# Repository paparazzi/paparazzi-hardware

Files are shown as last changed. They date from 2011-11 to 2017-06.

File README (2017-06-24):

#
#   $Id: README 6372 2010-11-07 00:50:29Z esden $
#   Copyright (C) 2004 Pascal Brisset, Antoine Drouin
#
# This file is part of paparazzi.
#
# paparazzi is free software; you can redistribute it and/or modify
# it under the terms of the GNU General Public License as published by
# the Free Software Foundation; either version 2, or (at your option)
# any later version.
#
# paparazzi is distributed in the hope that it will be useful,
# but WITHOUT ANY WARRANTY; without even the implied warranty of
# MERCHANTABILITY or FITNESS FOR A PARTICULAR PURPOSE.  See the
# GNU General Public License for more details.
#
# You should have received a copy of the GNU General Public License
# along with paparazzi; see the file COPYING.  If not, write to
# the Free Software Foundation, 59 Temple Place - Suite 330,
# Boston, MA 02111-1307, USA.  
# 

License:
--------
All PCB CAD files are released under GNU General Public License version 2 or
newer if not stated otherwise.

Older revisions:
----------------
This is a cleaned up repository that does not contain all the history of the
files. For older revisions please check the SVN repository on Savannah:
http://svn.savannah.nongnu.org/viewvc/paparazzi-hardware/trunk/?root=paparazzi

Techno:
-------
PCBs are 4 layers boards.
  They can be ordered from companies like eurocircuits (www.eurocircuits.com).
  I solder the components with a fine temperatue controlled iron. The IMU board 
  contains BGA gyros which will require some sort hot hot air method.

Tools:
  This files are produced using Eagle (www.cadsoft.de) version 4.11 for Linux.
  gerbmerge (http://claymore.engineer.gvsu.edu/~steriana/Python/gerbmerge/) is a
  free gerber panelisation tool. gerbv (http://gerbv.sourceforge.net) is a free
  gerber viewer. eagle3d ( http://www.matwei.de/doku.php?id=en:eagle3d:eagle3d )
  is a tool that allows generation of povray views of the boards.

Outputs:
  We use the eagle batch CAM processor to generate various outputs.
  type "make gerber" to generate gerber.
  type "make printable" to generate postscript and pdf. 
  they will be put in a printable subdirectory in each subdirectory. 

Directory content:
------------------
panel: 
  Contains configuration files used in conjunction with gerbmerge to produce a pannel
  to be sent to the PCB manufacturer (eurocircuits). A panel is a big PCB containing several smaller PCB.
  It allows you to choose which boards you want for your particular system.

controller: 
  This are the paparazzi controller boards.

sensors:

tools:

lib: 
  contains eagle library parts for components not found in the standard eagle library.

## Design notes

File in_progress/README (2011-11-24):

 This directory contains in progress project an some finished development board I made to test different parts

adxrs300_breakout.sch : breakout board for adxrs300 gyro evaluation
AMI_601.sch : breakout board for AMI601 magnetometer
current_probe.sch : some current sensor I don't remember about
ir_single_long.sch
ir_single_slim.sch
lipo_connector.sch
olimex_add_on.sch
pth_supply.sch
pth_supply_servos_molex.sch
pth_supply_servos.sch
test_2620.sch
test_filter.sch
test_usb_hub.sch
tiny4l_18_1_99.sch
vor_add_on.sch
xbee.sch

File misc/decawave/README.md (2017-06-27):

Decawave Modules
================

Boards:
------

 - MiniTag: A minimal weight arduino + decawave

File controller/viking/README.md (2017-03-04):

# Viking Motorsports Engine Control Unit

The latest version is `ECU v1.0` which corresponds to `v_0.2` board files.  More info can be found in https://wiki.paparazziuav.org/wiki/VMS_ECU

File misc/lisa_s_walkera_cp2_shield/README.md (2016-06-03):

This is a prototype. Current status:

* Only connectors are used, the rest is cut off.
* No decent GND connection.
* Polarity of tail rotor is reversed, need to exchange wires in the molex-connector.

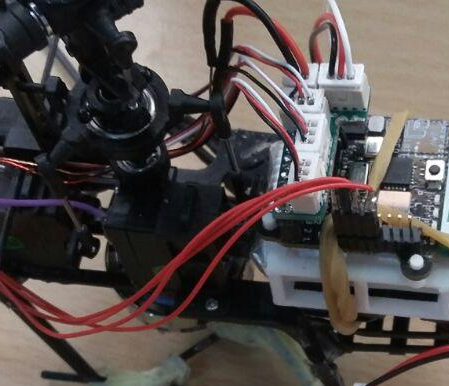
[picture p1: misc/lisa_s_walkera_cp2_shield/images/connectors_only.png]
Connectors only


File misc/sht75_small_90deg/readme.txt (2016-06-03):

Adapter board for the Sensirion SHT75 digital humidity and temperature
sensor, 90 degrees through-hole version.

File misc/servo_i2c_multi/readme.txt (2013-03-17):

This board combines a MS5611 pressure sensor, a multi-I2C connector, a 3.3V to 5V I2C level shifter and a JR servo connector.

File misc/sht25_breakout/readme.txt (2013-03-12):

Adapter board for the Sensirion SHT21/25 digital humidity and temperature
sensor.

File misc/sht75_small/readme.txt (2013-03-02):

Adapter board for the Sensirion SHT75 digital humidity and temperature
sensor.

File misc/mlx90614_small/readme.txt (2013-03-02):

Sensor board for Melexis MLX90614 infrared thermometer.

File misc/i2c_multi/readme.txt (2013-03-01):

This board is designed to connect multiple I2C sensors to one autopilot.
It was mainly used in meteorological applications.

R1 and R2 are optional and should not be populated if the autopilot is
already equipped with pull-up resistors (as in Tiny/TWOG/Lisa/...).

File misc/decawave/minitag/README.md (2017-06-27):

DM1000 + Arduino Mini Pro 3.3V/8MHz
===================================

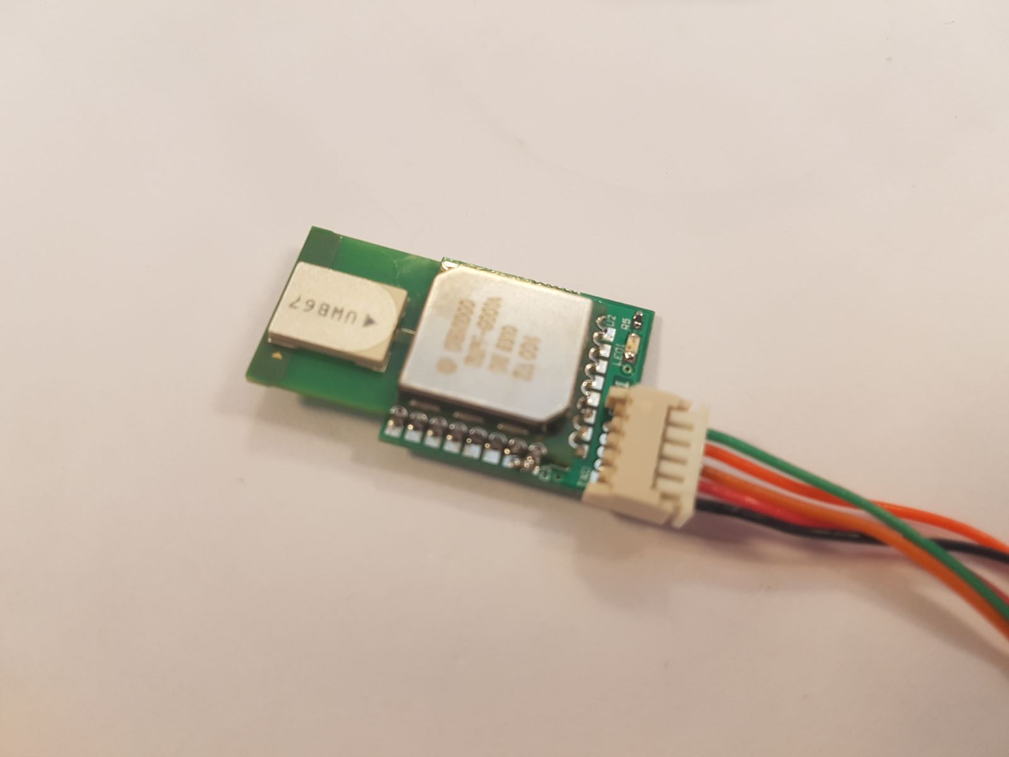
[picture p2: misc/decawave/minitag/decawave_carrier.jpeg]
Decawave Arduino


Discription:
-----------

 - Arduino Mini Pro 3.3V
 - flash elf file (bootloader+fuses) via ISP
 - afterwards the board can be programmed via arduino via serial
 - See schematics for Arduino pin numbers
 - See gerber for production

Licence:
--------

 - Hardware is released under **CC-BY-SA**

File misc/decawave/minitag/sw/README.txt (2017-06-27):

DECAWAVE ARDUINO
----------------

Arduino PRO Mini 328P 8MHz

---------

IRQ = 2

RST = 9

CS = 10
MOSI = 11
MISO = 12
SCK = 13

LED = 14 (A0)

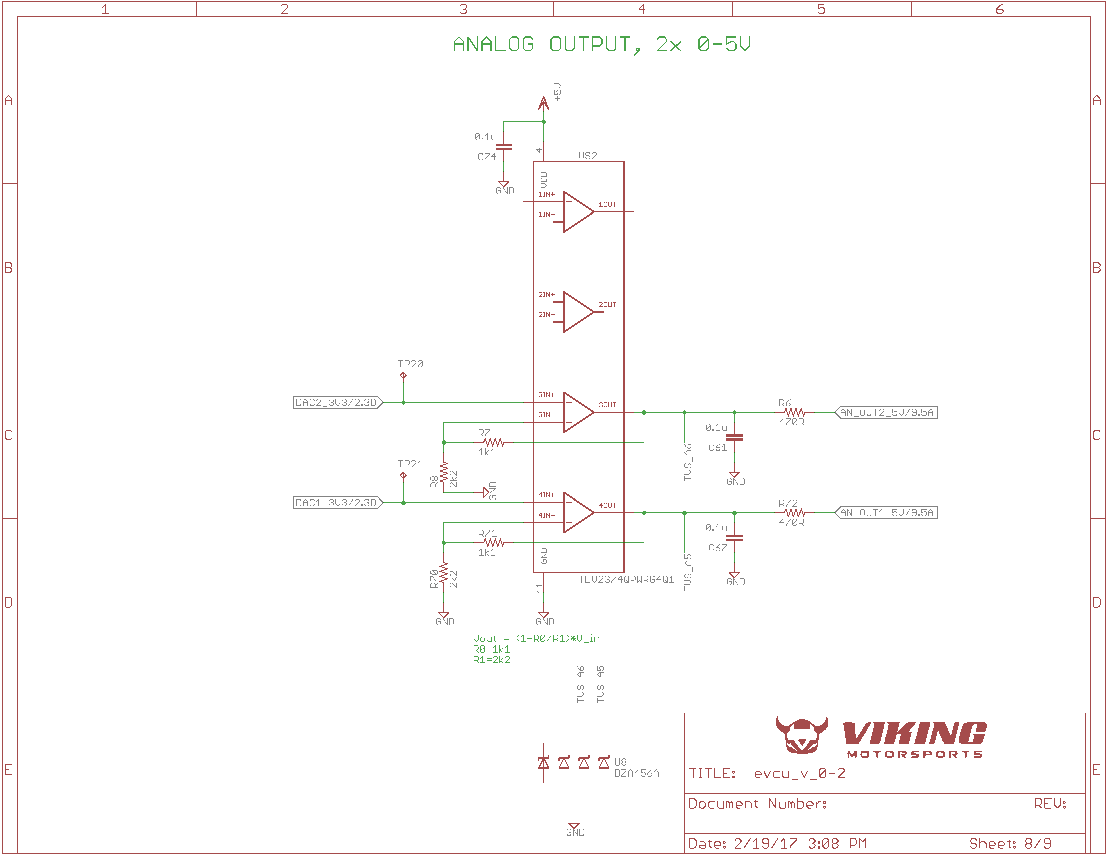
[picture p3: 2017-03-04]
controller/viking/Schematics/ecu_schematics_8.png

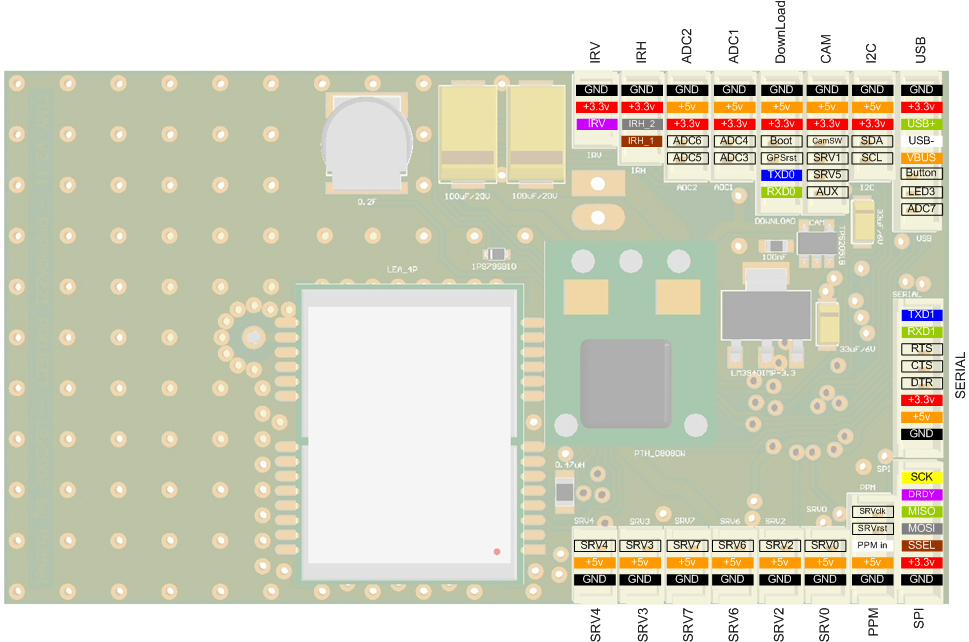
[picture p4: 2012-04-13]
controller/tiny/v2.11/Assembly/Tiny_v2-11_pinout.png

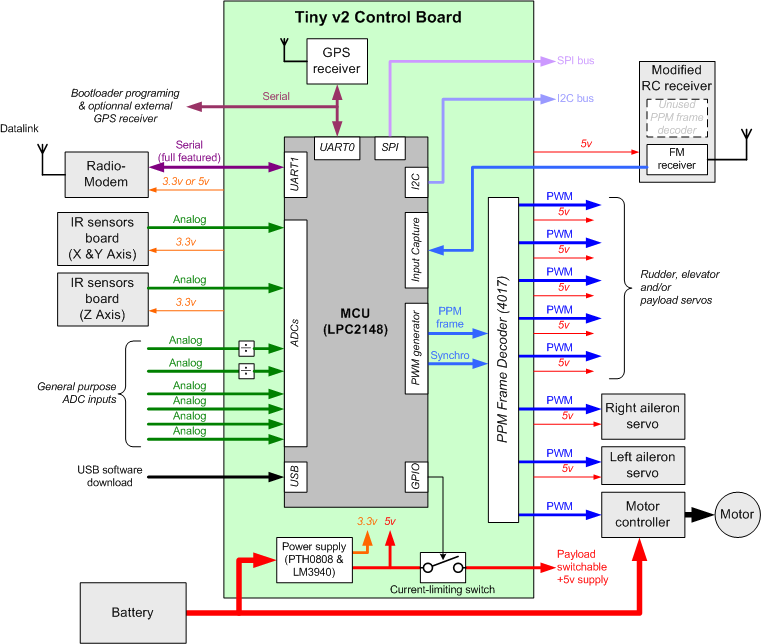
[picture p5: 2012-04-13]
controller/tiny/v2.11/Tiny_v2_11_Architecture.png

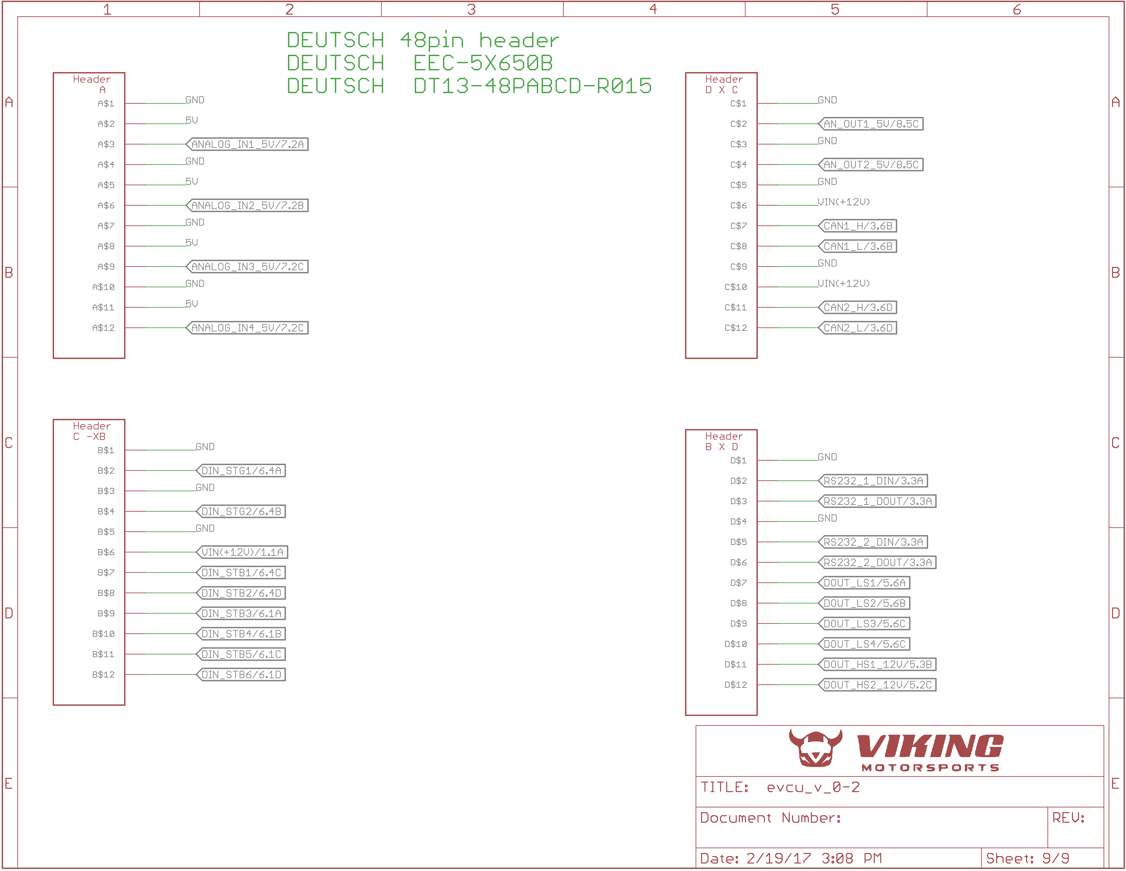
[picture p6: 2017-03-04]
controller/viking/Schematics/ecu_pinout.png

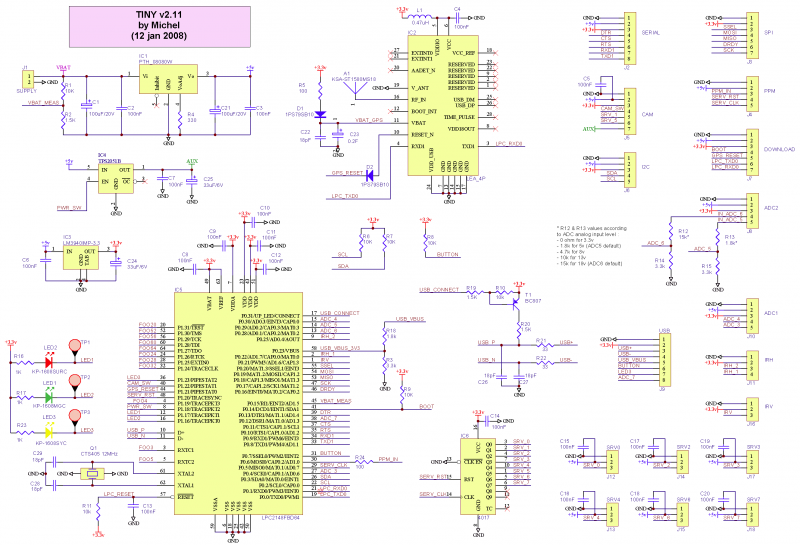
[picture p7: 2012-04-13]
controller/tiny/v2.11/Tiny_v2-11_Schematic.png

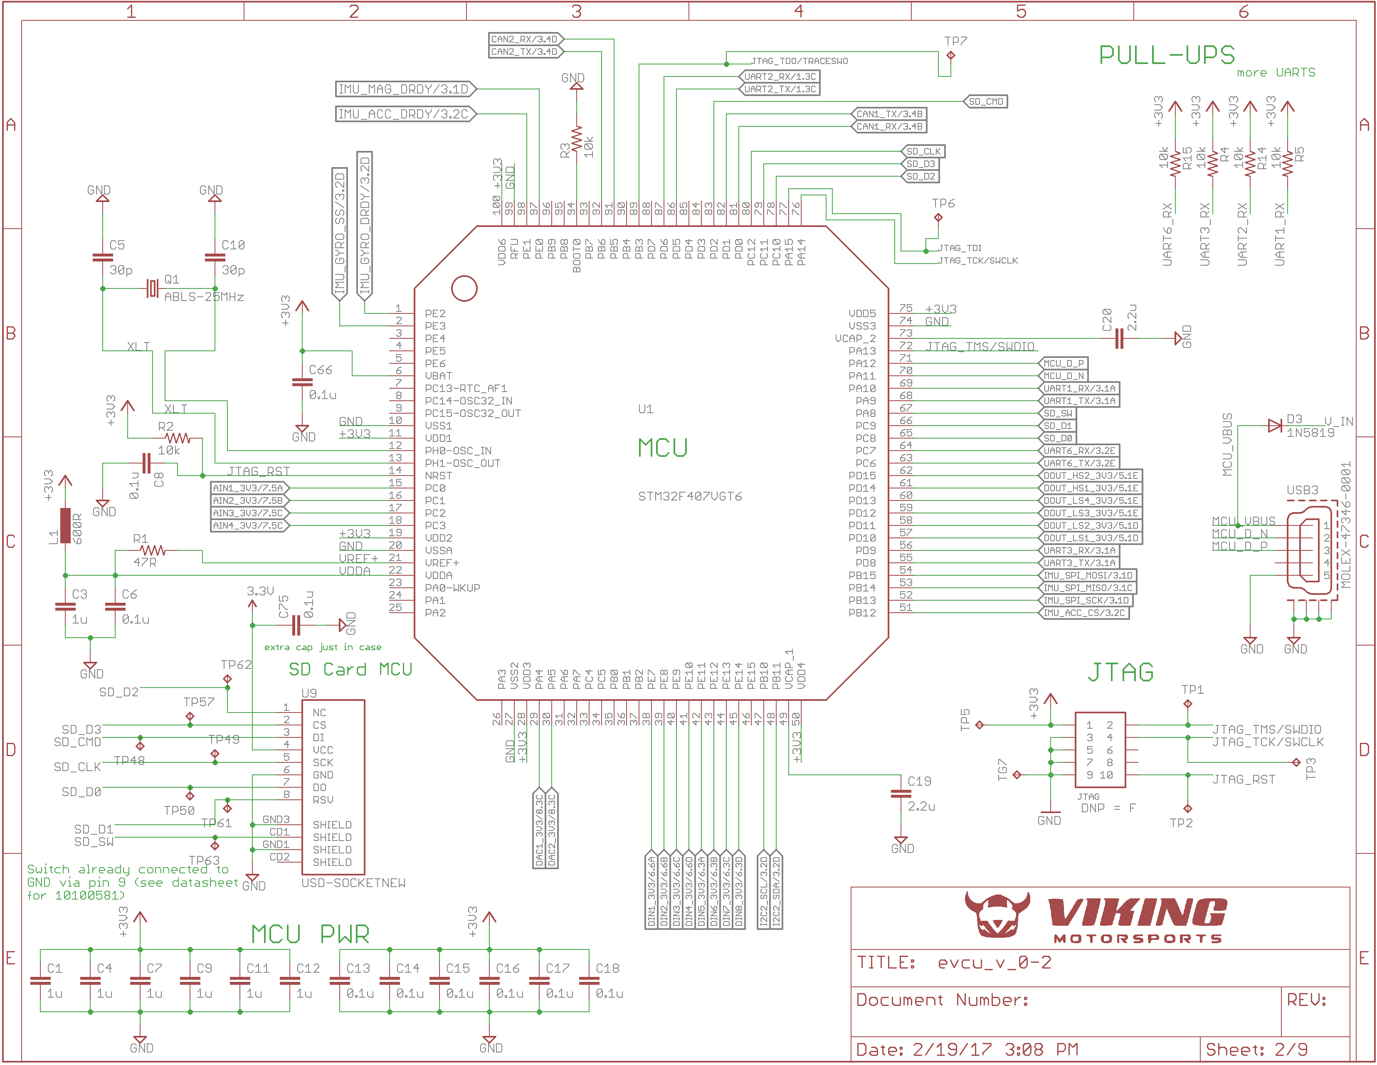
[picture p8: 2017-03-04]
controller/viking/Schematics/ecu_schematics_2.png

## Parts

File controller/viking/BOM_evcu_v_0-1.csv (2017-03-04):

Qty | Value | Device | Package | Parts | Description | DIGIKEY | DM | DNP | DR | DX | DY | MF | MPN | OC_FARNELL | OC_NEWARK | PACKAGE | PARTNO | SHEETNO | SUPPLIER | TP_SIGNAL_NAME
1 | 2920L185DR | 2920L | 2920L | PTC1
1 | 330R | R-US_R0603 | R0603 | R9 | RESISTOR | American symbol
1 | 36-2998-ND | COIN_CELL_6.8MM | BATTERY_6.8MM-2998 | B1
1 | 47R | R-US_R0603 | R0603 | R1 | RESISTOR | American symbol
1 | 600R | INDUCTOR-0603 | 0603-IND | L1
1 | 600R 1A | FB0603 | C0603 | FB9
1 | 74AHC1G126DCK | 74AHC1G126DCK | SC70-5 | IC4 | Single Bus Buffer Gate With 3-State Outputs
1 | ABLS-25MHz | CSM-7X-DU | CSM-7X-DU | Q1 | SMD CRYSTAL |  |  |  |  |  |  |  |  | unknown | unknown
1 | ASPIRIN | ASPIRIN | ASPIRIN_1 | IMU |  |  |  |  |  |  |  |  |  |  |  |  | ASP6000
1 | B360B-13-F | DIODE-SMB | SMB | D1 | DIODE
1 | DEUTSCH_48_PIN | DEUTSCH_48_PIN | DEUTSCH_48_PIN | U$5
1 | EDISON_CONNECTOR_SEGMENTED | EDISON_CONNECTOR_SEGMENTED | EDISON_DAUGHTER | E_1
1 | FT232RL | FT232RL | SSOP28 | IC3 | Source: http://www.ftdichip.com/Documents/DataSheets/DS_FT232R_v104.pdf |  |  |  |  |  |  |  | FT232RL | 1146032 | 91K9918
1 | GPS_UBLOX | GPS_UBLOX | GPS_UBLOX | U$3
1 | GREEN | LED0603 | D0603 | D2 |  |  | 0 |  | 90 | 57.2 | 1.8 |  |  |  |  |  |  | 4
1 | OKI-78SR-3.3/1.5-W36-C | OKI-78SR-3.3/1.5-W36-C | OKI-78SR | U$9
1 | OKI-78SR-5/1.5-W36-C | OKI-78SR-5/1.5-W36-C | OKI-78SR | U$1
1 | PIN_HDR_EDG_1.27MM_5-2 | CONN_5-2-FTSH-V | FTSH-105-DV | JTAG |  |  |  | T |  |  |  |  |  |  |  |  | conn-smd-0.05in-5-2
1 | SMBJ20CA-TR | SUPPRESSOR-SMBJ | SMBJ | TVS1 | Suppressor diode |  |  |  |  |  |  |  |  |  |  |  | SM30T35AY
1 | STM32F207VC | STM32F207VC | LQFP100 | U1 | STM32F207VC
1 | TRS3232EQPWRQ1 | TRS3232EQPWRQ1 | SOP65P640X120-16N | U2 | RS-232 LINE DRIVER/RECEIVER | 296-24863-1-ND |  |  |  |  |  |  | TRS3232EQPWRQ1 | 0 | 09R6724 | TSSOP-16 |  |  | Texas Instruments
2 | 100p | C-EUC0603 | C0603@1 | C58 | C59 | CAPACITOR | European symbol
2 | 10u | 25V | X5R | C-EUC0603 | C0603@1 | C50 | C53 | CAPACITOR | European symbol
2 | 120R | 1% | R-US_R0603 | R0603 | R64 | R65 | RESISTOR | American symbol
2 | 2.2u | C-EUC0603 | C0603@1 | C19 | C20 | CAPACITOR | European symbol
2 | 22u | C-USC1206 | C1206 | C26 | C27 | CAPACITOR | American symbol
2 | 2k43 | R-US_R0603 | R0603 | R31 | R32 | RESISTOR | American symbol
2 | 30p | C-EUC0603 | C0603@1 | C5 | C10 | CAPACITOR | European symbol
2 | 41k7 | R-US_R0603 | R0603 | R44 | R45 | RESISTOR | American symbol
2 | BTS3405G | BTS3405G | SOIC8 | U3 | U13 | Smart Low-Side Power Switch
2 | BZA456A | BZA456A | SOT457R_PHILIPS | U8 | U16 | BZA456A
2 | ISO1050DUB | ISO1050DUB | DUB-R-PDSO-G8 | IC1 | IC2 | ISOLATED CAN TRANSCEIVER |  |  |  |  |  |  |  | ISO1050DUBR | 1755712 | 14R9899
2 | ISP452 | ISP452 | SOT223-W | U4 | U12 | ISP 452
2 | MOLEX-47346-0001 | MOLEX-47346-0001 | MOLEX-47364-0001 | USB1 | USB2 | MICRO USB B | BOTTOM MOUNT
2 | R1SE | R1SE | R1SE | U$7 | U$8
2 | TLV2374QPWRG4Q1 | TLV2374QPWRG4Q1 | TSSOP14 | U$2 | U$6
2 | USD-SOCKETNEW | USD-SOCKETNEW | MICRO-SD-SOCKET-PP | U9 | U14 | microSD Socket
3 | TXB0108 | TXB0108 | UFDFN-20 | U7 | U17 | U19
4 | 74LVC2G17 | 74LVC2G17 | SOT363_INFINEON | U5 | U6 | U10 | U11 | 74LVC2G17
6 | 1k1 | R-US_R0603 | R0603 | R7 | R20 | R25 | R26 | R28 | R71 | RESISTOR | American symbol
6 | 2k2 | R-US_R0603 | R0603 | R8 | R22 | R27 | R29 | R30 | R70 | RESISTOR | American symbol
6 | DK:MMBT3904LT1GOSCT-ND | -NPN-SOT23-EBC | SOT23-EBC | T1 | T2 | T3 | T4 | T5 | T6 | NPN Transistror
7 | 1u | C-EUC0603 | C0603@1 | C1 | C3 | C4 | C7 | C9 | C11 | C12 | CAPACITOR | European symbol
7 | 4k7 | R-US_R0603 | R0603 | R10 | R35 | R38 | R43 | R55 | R60 | R63 | RESISTOR | American symbol
8 | 1000p | C-EUC0603 | C0603@1 | C41 | C42 | C43 | C44 | C45 | C46 | C47 | C48 | CAPACITOR | European symbol
8 | 1k | R-US_R0603 | R0603 | R39 | R40 | R48 | R49 | R50 | R51 | R56 | R57 | RESISTOR | American symbol
8 | 470R | R-US_R0603 | R0603 | R6 | R16 | R17 | R18 | R52 | R53 | R54 | R72 | RESISTOR | American symbol
23 | 10k | R-US_R0603 | R0603 | R2 | R3 | R4 | R5 | R11 | R14 | R15 | R19 | R21 | R23 | R24 | R33 | R34 | R36 | R37 | R41 | R42 | R46 | R47 | R58 | R59 | R61 | R62 | RESISTOR | American symbol
43 | 0.1u | C-EUC0603 | C0603@1 | C2 | C6 | C8 | C13 | C14 | C15 | C16 | C17 | C18 | C21 | C22 | C23 | C24 | C25 | C28 | C29 | C30 | C32 | C33 | C35 | C36 | C37 | C38 | C39 | C40 | C49 | C51 | C52 | C54 | C55 | C56 | C57 | C61 | C62 | C63 | C64 | C65 | C66 | C67 | C68 | C69 | C70 | C71 | CAPACITOR | European symbol
63 | TPB1 | 27 | TPB1 | 27 | B1 | 27 | TG1 | TG2 | TG3 | TG4 | TG5 | TG6 | TP1 | TP2 | TP3 | TP4 | TP5 | TP6 | TP7 | TP8 | TP9 | TP10 | TP11 | TP12 | TP13 | TP14 | TP15 | TP16 | TP17 | TP18 | TP19 | TP20 | TP21 | TP22 | TP23 | TP24 | TP25 | TP26 | TP27 | TP28 | TP29 | TP30 | TP31 | TP32 | TP33 | TP34 | TP35 | TP36 | TP37 | TP38 | TP39 | TP40 | TP41 | TP42 | TP43 | TP44 | TP45 | TP46 | TP47
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

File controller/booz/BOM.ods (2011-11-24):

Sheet: INTRODUCTION
Sheet | Description
MAIN
IMU
GPS
COMBINED | The individual parts list on one sheet
COMBINED ORDER | CSV file suitable for import at https://ordering.digikey.com/RegisteredUser/TextFileImport.aspx
DIGIKEY BOM | BOM (export as CSV) Template suitable for upload at https://ordering.digikey.com/RegisteredUser/OrderFileUpload.aspx
 |  | BOM Quantity 1 | 1
 |  | BOM Quantity 2 | 2
 |  | BOM Quantity 3 | 3
 |  | Combined Order Quantity | 1

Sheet: MAIN
Qty | Value | Device | Comment | Part Number | MOQ/MULT
1 | 1.5k | R-US_R0603 | R19 | 541-1.50KHCT-ND | 10
2 | 1.5uF | C-EUC0805 | C24, C34 | 399-3121-1-ND | 10
1 | 1.8k | R-US_R0603 | R9 | 541-1.80KHCT-ND | 10
6 | 1k | R-US_R0603 | R2, R4, R13, R15, R16, R22 | 541-1.00KHCT-ND | 10
1 | 2.2uF/Low ESR | C-EUC0603 | C16 | 490-4520-1-ND | 10
1 | 3.3k | R-US_R0603 | R8 | 541-3.30KHCT-ND | 10
1 | 3.9k | R-US_R0603 | R3 | 541-3.90KHCT-ND | 10
8 | 0/DNP | R-US_R0603 | R24, R26, R27, R31, R32, R48, R41, R42 | 541-0.0GCT-ND | 10
9 | 4.7k | R-US_R0603 | R1, R28, R29, R33, R34, R45, R46, R43, R44 | 541-4.70KHCT-ND | 10
1 | 4.7uF/10V/Low ESR | C-EUC0805K | C18 | 587-1442-1-ND | 10
4 | 10k | R-US_R0603 | R7, R35, R36, R37 | 541-10.0KHCT-ND | 10
1 | 10nF/16V | C-EUC0603K | C19 | PCC1750CT-ND | 1
1 | 680R | R-US_R0603 | R21 | 541-680HCT-ND | 10
1 | 560R | R-US_R0603 | R20 | 541-560HCT-ND | 10
1 | 27k | R-US_R0603 | R10 | 541-27.0KHCT-ND | 10
4 | 18pF | C-EUC0603 | C7, C8, C28, C29 | 399-1052-1-ND | 10
1 | 22uF/10V | CPOL-EUCT3216 | C17 | 718-1304-1-ND | 1
2 | 33R | R-US_R0603 | R17, R18 | 541-33.0HCT-ND | 10
1 | 33nF | C-EUC0805K | C25 | 587-1125-1-ND | 10
3 | 33uF/6V | CPOL-EUCT3216 | C6, C38, C40 | 399-4719-1-ND | 1
2 | 100R | R-US_R0603 | R12, R23 | 541-100HCT-ND | 10
22 | 100nF | C-EUC0603 | C2, C4, C5, C9, C10, C11, C12, C13, C14, C15, C20, C21, C22, C23, C26, C27, C30, C33, C35, C36, C37, C39 | 399-5089-1-ND | 10
1 | 100uF/20V | CPOL-EUSMCD | C1 | 478-1724-1-ND | 1
1 | 120k | R-US_R0603 | R11 | 541-120KHCT-ND | 10
3 | 200k | R-US_R0603 | R25, R30, R47 | P200KHCT-ND | 10
1 | 220uF/10V | CPOL-EUSMCD | C3 | 478-3929-1-ND | 1
1 | 348R | R-US_R0603 | R14 | 541-348HCT-ND | 10
1 | 390R | R-US_R0603 | R5 | 541-390HCT-ND | 10
1 | 12K | R-US_R0603 | R6 | 541-12.0KHCT-ND | 10
1 | 53047-12 | 53047-12 | IMU | WM1741-ND | 1
5 | 53261-02 | 53261-02 | MC2, MC3, MC_1, MC_4, PS | WM7620CT-ND | 1
1 | 53261-03 | 53261-03 | RC | WM7621CT-ND | 1
1 | 53261-05 | 53261-05 | UART_1 | WM7623CT-ND | 1
1 | 53261-06 | 53261-06 | UART_0 | WM7624CT-ND | 1
1 | 53261-07 | 53261-07 | CAM | WM7625CT-ND | 1
2 | 53261-08 | 53261-08 | GPS, SPI_0 | WM7626CT-ND | 1
1 | AD8552RU | AD8552RU | U$5 | AD8552ARUZ-ND | 1
1 | CRYSTAL_CTS | CRYSTAL_CTS | U$4 | CTX639CT-ND | 1
1 | DDTA143 | MUN2111T1 | Q1 | DDTA143ZCA-FDICT-ND | 1
1 | LM317MBDT | LM317MBDT | REG6V5A | LM317MDTXFSCT-ND | 1
1 | LM3940IMP-3.3 | LM3940IMP-3.3 | REG3V3D | LM3940IMP-3.3CT-ND | 1
1 | LM4041SC70 | LM4041SC70 | U$10 | LM4041CIM7-ADJCT-ND | 1
1 | LP2992 | MIC5219BM5 | REG5VA | LP2992AIM5-5.0CT-ND | 1
1 | LPC2148 | LPC2148 | U$1 | 568-1765-ND | 1
1 | LTC2485 | LTC2485 | U$9 | LTC2485CDD#PBF-ND | 1
1 | MINI-USB-UX60-MB-5ST | MINI-USB-UX60-MB-5ST | X5 | H2959CT-ND | 1
1 | MPX6115 | MPX6115 | U$2 | From Freescale
2 | PCA9306DP | PCA9306DP | LT_I2C, U$11 | 568-4214-1-ND | 1
1 | PTHTH | PTHTH | REG5VD | 296-20432-ND | 1
1 | R1 | R-US_R0603 | R40 | ???
1 | R2 | R-US_R0603 | R39 | ???
4 | RED | LEDCHIP-LED0805 | LED1,LED2,LED3,LED4 | P11505CT-ND | 1
1 | RS | R-US_R0603 | R38 | ???
4 | SOLDER_PAD150_75 | SOLDER_PAD150_75 | BAT_IN, BAT_IN1, GND_IN, GND_IN1 | N/A
3 | SW_PBST | SW_PBST | U$6, U$7, U$14 | SW1020CT-ND | 1
1 | SW_PB_GNDRT/A | SW_PB_GNDRT/A | U$3 | SW1023CT-ND | 1
2 | TPS2051B | TPS2051B | U$12, U$13 | 296-21265-1-ND | 1
1 | TXS0102DCU | TXS0102DCU | U$8 | 296-21931-1-ND | 1
1 | 24AA256 | 24AA128ST | IC1 | 24AA256-I/ST-ND | 1

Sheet: IMU
Qty | Value | Device | Comment | Part Number | MOQ/MULT
6 | 0/DNP | R-US_R0603 | R8, R9, R10, R15, xz_R1, yz_R5 | 541-0.0GCT-ND | 10
2 | 2.2uF/Low ESR | C-EUC0603K | C22, C24 | 490-4520-1-ND | 10
3 | 4.7uF/10V/Low ESR | C-EUC0805K | C25, C26, C21 | 587-1442-1-ND | 10
1 | 4.7k | R-US_R0603 | R16 | 541-4.70KHCT-ND | 10
3 | 10k | R-US_R0603 | R3, R5, R11 | 541-10.0KHCT-ND | 10
2 | 10nF | C-EUC0603K | C4, C15 | PCC1750CT-ND | 1
2 | 4.7uF | C-EUC0805 | C1, C16 | 587-1442-1-ND | 10
4 | 12k | R-US_R0603 | R6, R7, yz_R1, yz_R4 | 541-12.0KHCT-ND | 10
9 | 22nF | C-EUC0603K | C5, C8, C13, xz_C15, xz_C16, xz_C21, yz_C15, yz_C16, yz_C21 | 478-3722-1-ND | 10
1 | 39k/DNP | R-US_R0603 | R4 | 541-39.0KHCT-ND | 10
2 | 43R | R-US_R0603 | R1, R2 | 541-43.0HCT-ND | 10
3 | 47nF | C-EUC0603K | C12, xz_C20, yz_C20 | 478-3716-1-ND | 10
25 | 100nF | C-EUC0603K | C2, C3, C6, C7, C9, C10, C11, C14, C17, C18, C19, C20, C23, C33, C34, C27, xz_C17, xz_C18, xz_C19, yz_C17,yz_ C18,yz_ C19, yz_C23, yz_C33, yz_C34 | 399-5089-1-ND | 10
1 | 53261-12 | 53261-12 | X1 | WM7630CT-ND | 1
1 | 53047-12 | 53047-12 | X2 | WM1741-ND | 1
2 | ADXL320 | ADXL320 | U$2, yz_U$2 | ADXL320JCP-ND | 1
3 | ADXRS610 | ADXR | GYRO_Z, GYRO_X, GYRO_Y | ADXRS610BBGZ-RLCT-ND | 1
1 | IMU_XZ_2 | IMU_XZ_2 | XZ_BOARD | N/A | 1
1 | IMU_YZ_MAG_2 | IMU_YZ_MAG_2 | YZ_BOARD | N/A | 1
1 | LM3480 | LM3480 | U$3 | LM3480IM3-3.3CT-ND | 1
1 | LM4132 | LM4132 | U$1 | LM4132EMF-4.1CT-ND | 1
2 | LP2992 | MIC5219BM5 | IC1, IC3 | LP2992AIM5-5.0CT-ND | 1
1 | MAX1168CEEG+ | MAX1168 | ADC1 | From Maxim | 1
1 | MS2100 | MS2100 | MAG | From PNI | 1
1 | SEN_XY | SEN_XY | SEN_XY | From PNI | 1
1 | 25LC040A-I/ST | 25LC040ST | EEPROM | 25LC040A-I/ST-ND | 1

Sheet: GPS
Qty | Value | Device | Comment | Part Number | MOQ/MULT
3 | 150R | R-EU_R0603 | R1, R2, R3 | 541-150HCT-ND | 10
2 | 0/DNP | R-EU_R0603 | R4, R5 | 541-0.0GCT-ND | 10
2 | 22uF | CPOL-EUSMCB | C1, C3 | 495-2242-1-ND | 1
2 | 100nF | C-EUC0603 | C2, C4, C6 | 399-5089-1-ND | 10
1 | 470pF | C-EUC0603K | C5 | 311-1078-1-ND | 10
1 | 53047-08 | 53047-08 | X1 | WM1737-ND | 1
1 | BAT254 | DIODE-SOD110-R | D1 | 568-3412-1-ND | 1
1 | GND-GNDA | GND-GNDA | ~NUDEV~1 | N/A | 1
1 | GPS_PATCH_ANT | GPS_PATCH_ANT | ANT | N/A | 1
1 | LEA-5H-0-005 | LEA-4P | GPS | ??? | 1
1 | MIC5209 | MIC5209 | VREG1 | 576-1273-ND | 1
1 | PANA_GOLDCAP_J1ROUND | PANA_GOLDCAP_J1ROUND | C7 | P14163CT-ND | 1

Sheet: COMBINED
Qty | Comment | Part Number | MOQ/MULT
1 | m_R19 | 541-1.50KHCT-ND | 10
2 | m_C24/C34 | 399-3121-1-ND | 10
1 | m_R9 | 541-1.80KHCT-ND | 10
6 | m_R2/R4/R13/R15/R16/R22 | 541-1.00KHCT-ND | 10
1 | m_C16 | 490-4520-1-ND | 10
1 | m_R8 | 541-3.30KHCT-ND | 10
1 | m_R3 | 541-3.90KHCT-ND | 10
8 | m_R24/R26/R27/R31/R32/R48/R41/R42 | 541-0.0GCT-ND | 10
9 | m_R1/R28/R29/R33/R34/R45/R46/R43/R44 | 541-4.70KHCT-ND | 10
1 | m_C18 | 587-1442-1-ND | 10
4 | m_R7/R35/R36/R37 | 541-10.0KHCT-ND | 10
1 | m_C19 | PCC1750CT-ND | 1
1 | m_R21 | 541-680HCT-ND | 10
1 | m_R20 | 541-560HCT-ND | 10
1 | m_R10 | 541-27.0KHCT-ND | 10
4 | m_C7/C8/C28/C29 | 399-1052-1-ND | 10
1 | m_C17 | 718-1304-1-ND | 1
2 | m_R17/R18 | 541-33.0HCT-ND | 10
1 | m_C25 | 587-1125-1-ND | 10
3 | m_C6/C38/C40 | 399-4719-1-ND | 1
2 | m_R12/R23 | 541-100HCT-ND | 10
22 | m_C2/C4/C5/C9/C10/C11/C12/C13/C14/C15/C20/C21/C22/C23/C26/C27/C30/C33/C35/C36/C37/C39 | 399-5089-1-ND | 10
1 | m_C1 | 478-1724-1-ND | 1
1 | m_R11 | 541-120KHCT-ND | 10
3 | m_R25/R30/R47 | P200KHCT-ND | 10
1 | m_C3 | 478-3929-1-ND | 1
1 | m_R14 | 541-348HCT-ND | 10
1 | m_R5 | 541-390HCT-ND | 10
1 | m_R6 | 541-12.0KHCT-ND | 10
1 | m_IMU | WM1741-ND | 1
5 | m_MC2/MC3/MC_1/MC_4/PS | WM7620CT-ND | 1
1 | m_RC | WM7621CT-ND | 1
1 | m_UART_1 | WM7623CT-ND | 1
1 | m_UART_0 | WM7624CT-ND | 1
1 | m_CAM | WM7625CT-ND | 1
2 | m_GPS/SPI_0 | WM7626CT-ND | 1
1 | m_U$5 | AD8552ARUZ-ND | 1
1 | m_U$4 | CTX639CT-ND | 1
1 | m_Q1 | DDTA143ZCA-FDICT-ND | 1
1 | m_REG6V5A | LM317MDTXFSCT-ND | 1
1 | m_REG3V3D | LM3940IMP-3.3CT-ND | 1
1 | m_U$10 | LM4041CIM7-ADJCT-ND | 1
1 | m_REG5VA | LP2992AIM5-5.0CT-ND | 1
1 | m_U$1 | 568-1765-ND | 1
1 | m_U$9 | LTC2485CDD#PBF-ND | 1
1 | m_X5 | H2959CT-ND | 1
1 | m_U$2 | From Freescale | 0
2 | m_LT_I2C/U$11 | 568-4214-1-ND | 1
1 | m_REG5VD | 296-20432-ND | 1
1 | m_R40 | ??? | 0
1 | m_R39 | ??? | 0
4 | m_LED1,LED2,LED3,LED4 | P11505CT-ND | 1
1 | m_R38 | ??? | 0
4 | m_BAT_IN/BAT_IN1/GND_IN/GND_IN1 | N/A | 0
3 | m_U$6/U$7/U$14 | SW1020CT-ND | 1
1 | m_U$3 | SW1023CT-ND | 1
2 | m_U$12/U$13 | 296-21265-1-ND | 1
1 | m_U$8 | 296-21931-1-ND | 1
1 | m_IC1 | 24AA256-I/ST-ND | 1
6 | i_R8/R9/R10/R15/xz_R1/yz_R5 | 541-0.0GCT-ND | 10
2 | i_C22/C24 | 490-4520-1-ND | 10
3 | i_C25/C26/C21 | 587-1442-1-ND | 10
1 | i_R16 | 541-4.70KHCT-ND | 10
3 | i_R3/R5/R11 | 541-10.0KHCT-ND | 10
2 | i_C4/C15 | PCC1750CT-ND | 1
2 | i_C1/C16 | 587-1442-1-ND | 10
4 | i_R6/R7/yz_R1/yz_R4 | 541-12.0KHCT-ND | 10
9 | i_C5/C8/C13/xz_C15/xz_C16/xz_C21/yz_C15/yz_C16/yz_C21 | 478-3722-1-ND | 10
1 | i_R4 | 541-39.0KHCT-ND | 10
2 | i_R1/R2 | 541-43.0HCT-ND | 10
3 | i_C12/xz_C20/yz_C20 | 478-3716-1-ND | 10
25 | i_C2/C3/C6/C7/C9/C10/C11/C14/C17/C18/C19/C20/C23/C33/C34/C27/xz_C17/xz_C18/xz_C19/yz_C17,yz_ C18,yz_ C19/yz_C23/yz_C33/yz_C34 | 399-5089-1-ND | 10
1 | i_X1 | WM7630CT-ND | 1
1 | i_X2 | WM1741-ND | 1
2 | i_U$2/yz_U$2 | ADXL320JCP-ND | 1
3 | i_GYRO_Z/GYRO_X/GYRO_Y | ADXRS610BBGZ-RLCT-ND | 1
1 | i_XZ_BOARD | N/A | 1
1 | i_YZ_BOARD | N/A | 1
1 | i_U$3 | LM3480IM3-3.3CT-ND | 1
1 | i_U$1 | LM4132EMF-4.1CT-ND | 1
2 | i_IC1/IC3 | LP2992AIM5-5.0CT-ND | 1
1 | i_ADC1 | From Maxim | 1
1 | i_MAG | From PNI | 1
1 | i_SEN_XY | From PNI | 1
1 | i_EEPROM | 25LC040A-I/ST-ND | 1
3 | g_R1/R2/R3 | 541-150HCT-ND | 10
2 | g_R4/R5 | 541-0.0GCT-ND | 10
2 | g_C1/C3 | 495-2242-1-ND | 1
2 | g_C2/C4/C6 | 399-5089-1-ND | 10
1 | g_C5 | 311-1078-1-ND | 10
1 | g_X1 | WM1737-ND | 1
1 | g_D1 | 568-3412-1-ND | 1
1 | g_~NUDEV~1 | N/A | 1
1 | g_ANT | N/A | 1
1 | g_GPS | ??? | 1
1 | g_VREG1 | 576-1273-ND | 1
1 | g_C7 | P14163CT-ND | 1
225

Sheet: COMBINED ORDER
Quantity | Part | Comment
10 | 541-1.50KHCT-ND | m_R19
10 | 399-3121-1-ND | m_C24/C34
10 | 541-1.80KHCT-ND | m_R9
10 | 541-1.00KHCT-ND | m_R2/R4/R13/R15/R16/R22
10 | 490-4520-1-ND | m_C16
10 | 541-3.30KHCT-ND | m_R8
10 | 541-3.90KHCT-ND | m_R3
10 | 541-0.0GCT-ND | m_R24/R26/R27/R31/R32/R48/R41/R42
10 | 541-4.70KHCT-ND | m_R1/R28/R29/R33/R34/R45/R46/R43/R44
10 | 587-1442-1-ND | m_C18
10 | 541-10.0KHCT-ND | m_R7/R35/R36/R37
1 | PCC1750CT-ND | m_C19
10 | 541-680HCT-ND | m_R21
10 | 541-560HCT-ND | m_R20
10 | 541-27.0KHCT-ND | m_R10
10 | 399-1052-1-ND | m_C7/C8/C28/C29
1 | 718-1304-1-ND | m_C17
10 | 541-33.0HCT-ND | m_R17/R18
10 | 587-1125-1-ND | m_C25
3 | 399-4719-1-ND | m_C6/C38/C40
10 | 541-100HCT-ND | m_R12/R23
30 | 399-5089-1-ND | m_C2/C4/C5/C9/C10/C11/C12/C13/C14/C15/C20/C21/C22/C23/C26/C27/C30/C33/C35/C36/C37/C39
1 | 478-1724-1-ND | m_C1
10 | 541-120KHCT-ND | m_R11
10 | P200KHCT-ND | m_R25/R30/R47
1 | 478-3929-1-ND | m_C3
10 | 541-348HCT-ND | m_R14
10 | 541-390HCT-ND | m_R5
10 | 541-12.0KHCT-ND | m_R6
1 | WM1741-ND | m_IMU
5 | WM7620CT-ND | m_MC2/MC3/MC_1/MC_4/PS
1 | WM7621CT-ND | m_RC
1 | WM7623CT-ND | m_UART_1
1 | WM7624CT-ND | m_UART_0
1 | WM7625CT-ND | m_CAM
2 | WM7626CT-ND | m_GPS/SPI_0
1 | AD8552ARUZ-ND | m_U$5
1 | CTX639CT-ND | m_U$4
1 | DDTA143ZCA-FDICT-ND | m_Q1
1 | LM317MDTXFSCT-ND | m_REG6V5A
1 | LM3940IMP-3.3CT-ND | m_REG3V3D
1 | LM4041CIM7-ADJCT-ND | m_U$10
1 | LP2992AIM5-5.0CT-ND | m_REG5VA
1 | 568-1765-ND | m_U$1
1 | LTC2485CDD#PBF-ND | m_U$9
1 | H2959CT-ND | m_X5
0 | From Freescale | m_U$2
2 | 568-4214-1-ND | m_LT_I2C/U$11
1 | 296-20432-ND | m_REG5VD
0 | ??? | m_R40
0 | ??? | m_R39
4 | P11505CT-ND | m_LED1,LED2,LED3,LED4
0 | ??? | m_R38
0 | N/A | m_BAT_IN/BAT_IN1/GND_IN/GND_IN1
3 | SW1020CT-ND | m_U$6/U$7/U$14
1 | SW1023CT-ND | m_U$3
2 | 296-21265-1-ND | m_U$12/U$13
1 | 296-21931-1-ND | m_U$8
1 | 24AA256-I/ST-ND | m_IC1
10 | 541-0.0GCT-ND | i_R8/R9/R10/R15/xz_R1/yz_R5
10 | 490-4520-1-ND | i_C22/C24
10 | 587-1442-1-ND | i_C25/C26/C21
10 | 541-4.70KHCT-ND | i_R16
10 | 541-10.0KHCT-ND | i_R3/R5/R11
2 | PCC1750CT-ND | i_C4/C15
10 | 587-1442-1-ND | i_C1/C16
10 | 541-12.0KHCT-ND | i_R6/R7/yz_R1/yz_R4
10 | 478-3722-1-ND | i_C5/C8/C13/xz_C15/xz_C16/xz_C21/yz_C15/yz_C16/yz_C21
10 | 541-39.0KHCT-ND | i_R4
10 | 541-43.0HCT-ND | i_R1/R2
10 | 478-3716-1-ND | i_C12/xz_C20/yz_C20
30 | 399-5089-1-ND | i_C2/C3/C6/C7/C9/C10/C11/C14/C17/C18/C19/C20/C23/C33/C34/C27/xz_C17/xz_C18/xz_C19/yz_C17,yz_ C18,yz_ C19/yz_C23/yz_C33/yz_C34
1 | WM7630CT-ND | i_X1
1 | WM1741-ND | i_X2
2 | ADXL320JCP-ND | i_U$2/yz_U$2
3 | ADXRS610BBGZ-RLCT-ND | i_GYRO_Z/GYRO_X/GYRO_Y
1 | N/A | i_XZ_BOARD
1 | N/A | i_YZ_BOARD
1 | LM3480IM3-3.3CT-ND | i_U$3
1 | LM4132EMF-4.1CT-ND | i_U$1
2 | LP2992AIM5-5.0CT-ND | i_IC1/IC3
1 | From Maxim | i_ADC1
1 | From PNI | i_MAG
1 | From PNI | i_SEN_XY
1 | 25LC040A-I/ST-ND | i_EEPROM
10 | 541-150HCT-ND | g_R1/R2/R3
10 | 541-0.0GCT-ND | g_R4/R5
2 | 495-2242-1-ND | g_C1/C3
10 | 399-5089-1-ND | g_C2/C4/C6
10 | 311-1078-1-ND | g_C5
1 | WM1737-ND | g_X1
1 | 568-3412-1-ND | g_D1
1 | N/A | g_~NUDEV~1
1 | N/A | g_ANT
1 | ??? | g_GPS
1 | 576-1273-ND | g_VREG1
1 | P14163CT-ND | g_C7
512

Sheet: DIGIKEY_BOM
Digi-Key Part Number | Manufacturer | Manufacturer Part Number | Customer Reference | Quantity 1 | Quantity 2 | Quantity 3
541-1.50KHCT-ND |  |  | m_R19 | 10 | 10 | 10
399-3121-1-ND |  |  | m_C24/C34 | 10 | 10 | 10
541-1.80KHCT-ND |  |  | m_R9 | 10 | 10 | 10
541-1.00KHCT-ND |  |  | m_R2/R4/R13/R15/R16/R22 | 10 | 20 | 20
490-4520-1-ND |  |  | m_C16 | 10 | 10 | 10
541-3.30KHCT-ND |  |  | m_R8 | 10 | 10 | 10
541-3.90KHCT-ND |  |  | m_R3 | 10 | 10 | 10
541-0.0GCT-ND |  |  | m_R24/R26/R27/R31/R32/R48/R41/R42 | 10 | 20 | 30
541-4.70KHCT-ND |  |  | m_R1/R28/R29/R33/R34/R45/R46/R43/R44 | 10 | 20 | 30
587-1442-1-ND |  |  | m_C18 | 10 | 10 | 10
541-10.0KHCT-ND |  |  | m_R7/R35/R36/R37 | 10 | 10 | 20
PCC1750CT-ND |  |  | m_C19 | 1 | 2 | 3
541-680HCT-ND |  |  | m_R21 | 10 | 10 | 10
541-560HCT-ND |  |  | m_R20 | 10 | 10 | 10
541-27.0KHCT-ND |  |  | m_R10 | 10 | 10 | 10
399-1052-1-ND |  |  | m_C7/C8/C28/C29 | 10 | 10 | 20
718-1304-1-ND |  |  | m_C17 | 1 | 2 | 3
541-33.0HCT-ND |  |  | m_R17/R18 | 10 | 10 | 10
587-1125-1-ND |  |  | m_C25 | 10 | 10 | 10
399-4719-1-ND |  |  | m_C6/C38/C40 | 3 | 6 | 9
541-100HCT-ND |  |  | m_R12/R23 | 10 | 10 | 10
399-5089-1-ND |  |  | m_C2/C4/C5/C9/C10/C11/C12/C13/C14/C15/C20/C21/C22/C23/C26/C27/C30/C33/C35/C36/C37/C39 | 30 | 50 | 70
478-1724-1-ND |  |  | m_C1 | 1 | 2 | 3
541-120KHCT-ND |  |  | m_R11 | 10 | 10 | 10
P200KHCT-ND |  |  | m_R25/R30/R47 | 10 | 10 | 10
478-3929-1-ND |  |  | m_C3 | 1 | 2 | 3
541-348HCT-ND |  |  | m_R14 | 10 | 10 | 10
541-390HCT-ND |  |  | m_R5 | 10 | 10 | 10
541-12.0KHCT-ND |  |  | m_R6 | 10 | 10 | 10
WM1741-ND |  |  | m_IMU | 1 | 2 | 3
WM7620CT-ND |  |  | m_MC2/MC3/MC_1/MC_4/PS | 5 | 10 | 15
WM7621CT-ND |  |  | m_RC | 1 | 2 | 3
WM7623CT-ND |  |  | m_UART_1 | 1 | 2 | 3
WM7624CT-ND |  |  | m_UART_0 | 1 | 2 | 3
WM7625CT-ND |  |  | m_CAM | 1 | 2 | 3
WM7626CT-ND |  |  | m_GPS/SPI_0 | 2 | 4 | 6
AD8552ARUZ-ND |  |  | m_U$5 | 1 | 2 | 3
CTX639CT-ND |  |  | m_U$4 | 1 | 2 | 3
DDTA143ZCA-FDICT-ND |  |  | m_Q1 | 1 | 2 | 3
LM317MDTXFSCT-ND |  |  | m_REG6V5A | 1 | 2 | 3
LM3940IMP-3.3CT-ND |  |  | m_REG3V3D | 1 | 2 | 3
LM4041CIM7-ADJCT-ND |  |  | m_U$10 | 1 | 2 | 3
LP2992AIM5-5.0CT-ND |  |  | m_REG5VA | 1 | 2 | 3
568-1765-ND |  |  | m_U$1 | 1 | 2 | 3
LTC2485CDD#PBF-ND |  |  | m_U$9 | 1 | 2 | 3
H2959CT-ND |  |  | m_X5 | 1 | 2 | 3
From Freescale |  |  | m_U$2 | 0 | 0 | 0
568-4214-1-ND |  |  | m_LT_I2C/U$11 | 2 | 4 | 6
296-20432-ND |  |  | m_REG5VD | 1 | 2 | 3
??? |  |  | m_R40 | 0 | 0 | 0
??? |  |  | m_R39 | 0 | 0 | 0
P11505CT-ND |  |  | m_LED1,LED2,LED3,LED4 | 4 | 8 | 12
??? |  |  | m_R38 | 0 | 0 | 0
N/A |  |  | m_BAT_IN/BAT_IN1/GND_IN/GND_IN1 | 0 | 0 | 0
SW1020CT-ND |  |  | m_U$6/U$7/U$14 | 3 | 6 | 9
SW1023CT-ND |  |  | m_U$3 | 1 | 2 | 3
296-21265-1-ND |  |  | m_U$12/U$13 | 2 | 4 | 6
296-21931-1-ND |  |  | m_U$8 | 1 | 2 | 3
24AA256-I/ST-ND |  |  | m_IC1 | 1 | 2 | 3
541-0.0GCT-ND |  |  | i_R8/R9/R10/R15/xz_R1/yz_R5 | 10 | 20 | 20
490-4520-1-ND |  |  | i_C22/C24 | 10 | 10 | 10
587-1442-1-ND |  |  | i_C25/C26/C21 | 10 | 10 | 10
541-4.70KHCT-ND |  |  | i_R16 | 10 | 10 | 10
541-10.0KHCT-ND |  |  | i_R3/R5/R11 | 10 | 10 | 10
PCC1750CT-ND |  |  | i_C4/C15 | 2 | 4 | 6
587-1442-1-ND |  |  | i_C1/C16 | 10 | 10 | 10
541-12.0KHCT-ND |  |  | i_R6/R7/yz_R1/yz_R4 | 10 | 10 | 20
478-3722-1-ND |  |  | i_C5/C8/C13/xz_C15/xz_C16/xz_C21/yz_C15/yz_C16/yz_C21 | 10 | 20 | 30
541-39.0KHCT-ND |  |  | i_R4 | 10 | 10 | 10
541-43.0HCT-ND |  |  | i_R1/R2 | 10 | 10 | 10
478-3716-1-ND |  |  | i_C12/xz_C20/yz_C20 | 10 | 10 | 10
399-5089-1-ND |  |  | i_C2/C3/C6/C7/C9/C10/C11/C14/C17/C18/C19/C20/C23/C33/C34/C27/xz_C17/xz_C18/xz_C19/yz_C17,yz_ C18,yz_ C19/yz_C23/yz_C33/yz_C34 | 30 | 60 | 80
WM7630CT-ND |  |  | i_X1 | 1 | 2 | 3
WM1741-ND |  |  | i_X2 | 1 | 2 | 3
ADXL320JCP-ND |  |  | i_U$2/yz_U$2 | 2 | 4 | 6
ADXRS610BBGZ-RLCT-ND |  |  | i_GYRO_Z/GYRO_X/GYRO_Y | 3 | 6 | 9
N/A |  |  | i_XZ_BOARD | 1 | 2 | 3
N/A |  |  | i_YZ_BOARD | 1 | 2 | 3
LM3480IM3-3.3CT-ND |  |  | i_U$3 | 1 | 2 | 3
LM4132EMF-4.1CT-ND |  |  | i_U$1 | 1 | 2 | 3
LP2992AIM5-5.0CT-ND |  |  | i_IC1/IC3 | 2 | 4 | 6
From Maxim |  |  | i_ADC1 | 1 | 2 | 3
From PNI |  |  | i_MAG | 1 | 2 | 3
From PNI |  |  | i_SEN_XY | 1 | 2 | 3
25LC040A-I/ST-ND |  |  | i_EEPROM | 1 | 2 | 3
541-150HCT-ND |  |  | g_R1/R2/R3 | 10 | 10 | 10
541-0.0GCT-ND |  |  | g_R4/R5 | 10 | 10 | 10
495-2242-1-ND |  |  | g_C1/C3 | 2 | 4 | 6
399-5089-1-ND |  |  | g_C2/C4/C6 | 10 | 10 | 10
311-1078-1-ND |  |  | g_C5 | 10 | 10 | 10
WM1737-ND |  |  | g_X1 | 1 | 2 | 3
568-3412-1-ND |  |  | g_D1 | 1 | 2 | 3
N/A |  |  | g_~NUDEV~1 | 1 | 2 | 3
N/A |  |  | g_ANT | 1 | 2 | 3
??? |  |  | g_GPS | 1 | 2 | 3
576-1273-ND |  |  | g_VREG1 | 1 | 2 | 3
P14163CT-ND |  |  | g_C7 | 1 | 2 | 3

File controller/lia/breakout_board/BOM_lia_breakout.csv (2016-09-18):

Qty | Value | Device | Package | Parts | Description | DNP | MFR-PN | PARTNO
4 |  | PINHD-1X4 | 1X04 | JP14, JP15, JP16, JP17 | PIN HEADER | T |  | conn-th-0.1in-4-1
1 |  | PINHD-1X6 | 1X06 | JP20 | PIN HEADER | T |  | conn-th-0.1in-6-1
2 |  | PINHD-1X7 | 1X07 | JP21, JP22 | PIN HEADER | T |  | conn-th-0.1in-7-1
8 | 0.1uF | CAP0603-CAP | 0603-CAP | C1, C2, C3, C6, C7, C9, C10, C12 | Capacitor
4 | 10uF | CAP_POL1206 | EIA3216 | C4, C5, C8, C11 | Capacitor Polarized
8 | 1K | RESISTOR0603-RES | 0603-RES | R1, R2, R3, R4, R5, R6, R7, R8 | Resistor
4 | CONN_3-1 | CONN_3-1 | SIP1X3_100 | J1, J2, J3, J4 |  |  |  | conn-th-0.1in-3-2-ra
4 | CONN_3-1 | CONN_3-1 | SIP1X3_100 | J5, J6, J7, J8 |  | T |  | conn-th-0.1in-3-2-ra
4 | FT232RLSSOP | FT232RLSSOP | SSOP28DB | U1, U2, U3, U5 | USB UART
4 | Green | LED0603 | LED-0603 | LED2, LED4, LED6, LED8 | LEDs
4 | Red | LED0603 | LED-0603 | LED1, LED3, LED5, LED7 | LEDs
4 | USB-SMD-NS | USB-SMD-NS | USB-MINIB-NOSTOP | X1, X2, X3, X4 | USB Connectors

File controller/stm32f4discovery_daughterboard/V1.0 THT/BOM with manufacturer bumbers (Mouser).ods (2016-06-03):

Part | Value | Footprint | Manufacturer Part | comment
3,2mm1 | MOUNTING_HOLE | mounting_hole_3,2mm
3,2mm2 | MOUNTING_HOLE | mounting_hole_3,2mm
3,2mm3 | MOUNTING_HOLE | mounting_hole_3,2mm
3,2mm4 | MOUNTING_HOLE | mounting_hole_3,2mm
ADC1 | CONN_12 | SIL-12
B1 | BUZZER_12.2X3.5 | buzzer_PS1240P02CT3 | PS1240P02CT3 (https://at.mouser.com/Search/ProductDetail.aspx)
BOOT0 | SW_PUSH | pushbutton_tactile | 1301.9301 (https://at.mouser.com/Search/ProductDetail.aspx?R=1301.9301virtualkey69300000virtualkey693-1301.9301)
C1 | 100n | C1 | C315C104M5U5TA7303 (https://at.mouser.com/Search/ProductDetail.aspx)
C2 | 100n | C1 | C315C104M5U5TA7303 (https://at.mouser.com/Search/ProductDetail.aspx)
C3 | 100n | C1 | C315C104M5U5TA7303 (https://at.mouser.com/Search/ProductDetail.aspx)
C4 | 100n | C1 | C315C104M5U5TA7303 (https://at.mouser.com/Search/ProductDetail.aspx)
C5 | 100n | C1 | C315C104M5U5TA7303 (https://at.mouser.com/Search/ProductDetail.aspx)
C6 | 100n | C1 | C315C104M5U5TA7303 (https://at.mouser.com/Search/ProductDetail.aspx)
C7 | CAPAPOL | C2V8 | ESS476M025AE2EA (https://at.mouser.com/Search/ProductDetail.aspx)
C8 | CAPAPOL | C2V8 | ESS476M025AE2EA (https://at.mouser.com/Search/ProductDetail.aspx)
C9 | 100n | C1 | C315C104M5U5TA7303 (https://at.mouser.com/Search/ProductDetail.aspx)
C10 | 100n | C1 | C315C104M5U5TA7303 (https://at.mouser.com/Search/ProductDetail.aspx)
D1 | DIODE | D3 | 1N5819 (https://at.mouser.com/Search/ProductDetail.aspx?R=1N5819virtualkey53310000virtualkey821-1N5819)
D2 | DIODE | D3 | 1N5819 (https://at.mouser.com/Search/ProductDetail.aspx?R=1N5819virtualkey53310000virtualkey821-1N5819)
D3 | DIODE | D3 | 1N5819 (https://at.mouser.com/Search/ProductDetail.aspx?R=1N5819virtualkey53310000virtualkey821-1N5819)
D4 | DIODE | D3 | 1N5819 (https://at.mouser.com/Search/ProductDetail.aspx?R=1N5819virtualkey53310000virtualkey821-1N5819)
D5 | DIODE | D3 | 1N5819 (https://at.mouser.com/Search/ProductDetail.aspx?R=1N5819virtualkey53310000virtualkey821-1N5819)
D6 | DIODE | D3 | 1N5819 (https://at.mouser.com/Search/ProductDetail.aspx?R=1N5819virtualkey53310000virtualkey821-1N5819)
D7 | DIODE | D3 | 1N5819 (https://at.mouser.com/Search/ProductDetail.aspx?R=1N5819virtualkey53310000virtualkey821-1N5819)
D8 | DIODE | D3 | 1N5819 (https://at.mouser.com/Search/ProductDetail.aspx?R=1N5819virtualkey53310000virtualkey821-1N5819)
D9 | DIODE | D3 | 1N5819 (https://at.mouser.com/Search/ProductDetail.aspx?R=1N5819virtualkey53310000virtualkey821-1N5819)
D10 | DIODE | D3 | 1N5819 (https://at.mouser.com/Search/ProductDetail.aspx?R=1N5819virtualkey53310000virtualkey821-1N5819)
D11 | DIODE | D3 | 1N5819 (https://at.mouser.com/Search/ProductDetail.aspx?R=1N5819virtualkey53310000virtualkey821-1N5819)
D12 | DIODE | D3 | 1N5819 (https://at.mouser.com/Search/ProductDetail.aspx?R=1N5819virtualkey53310000virtualkey821-1N5819)
D13 | DIODE | D3 | 1N5819 (https://at.mouser.com/Search/ProductDetail.aspx?R=1N5819virtualkey53310000virtualkey821-1N5819)
D14 | DIODE | D3 | 1N5819 (https://at.mouser.com/Search/ProductDetail.aspx?R=1N5819virtualkey53310000virtualkey821-1N5819)
D15 | DIODE | D3 | 1N5819 (https://at.mouser.com/Search/ProductDetail.aspx?R=1N5819virtualkey53310000virtualkey821-1N5819)
Drotek10DOF1 | CONN_5 | drotek10dof
I2C1 | CONN_4 | PIN_ARRAY_4x1
I2C2 | CONN_4 | PIN_ARRAY_4x1
I2C3 | CONN_4 | PIN_ARRAY_4x1
JP1 | JUMPER | Ujumper
JP2 | JUMPER | Ujumper
P1 | CONN_25X2 | pin_array_25x2
P2 | CONN_25X2 | pin_array_25x2
PWM/PPM/Spektrum1 | CONN_15X3 | in_array_15x3
R1 | 22k | R3 | MF1/4DC2202F (https://at.mouser.com/Search/ProductDetail.aspx)
R2 | 2k2 | R3 | MF1/4DCT52R2201F (https://at.mouser.com/Search/ProductDetail.aspx)
R3 | 22k | R3 | MF1/4DC2202F (https://at.mouser.com/Search/ProductDetail.aspx)
R4 | 2k2 | R3 | MF1/4DCT52R2201F (https://at.mouser.com/Search/ProductDetail.aspx)
R5 | 22k | R3 | MF1/4DC2202F (https://at.mouser.com/Search/ProductDetail.aspx)
R6 | 2k2 | R3 | MF1/4DCT52R2201F (https://at.mouser.com/Search/ProductDetail.aspx)
R7 | 22k | R3 | MF1/4DC2202F (https://at.mouser.com/Search/ProductDetail.aspx)
R8 | 2k2 | R3 | MF1/4DCT52R2201F (https://at.mouser.com/Search/ProductDetail.aspx)
R9 | 22k | R3 | MF1/4DC2202F (https://at.mouser.com/Search/ProductDetail.aspx)
R10 | 2k2 | R3 | MF1/4DCT52R2201F (https://at.mouser.com/Search/ProductDetail.aspx)
R11 | 22k | R3 | MF1/4DC2202F (https://at.mouser.com/Search/ProductDetail.aspx)
R12 | 2k2 | R3 | MF1/4DCT52R2201F (https://at.mouser.com/Search/ProductDetail.aspx)
R13 | 220 | R3 | MF1/4DCT52R2200F (https://at.mouser.com/Search/ProductDetail.aspx)
R14 | 470 | R3 | MF1/4DCT52R4700F (https://at.mouser.com/Search/ProductDetail.aspx)
R15 | 1k | R3
screw1 | CONN_3 | bornier3 | 20020316-H031B01LF (https://at.mouser.com/Search/ProductDetail.aspx)
screw2 | CONN_2 | bornier2
screw3 | CONN_2 | bornier2
SPI1 | CONN_6 | PIN_ARRAY-6X1
SPI2 | CONN_6 | PIN_ARRAY-6X1
SPI3 | CONN_6 | PIN_ARRAY-6X1
T1 | BC547 | TO92 | BC547CG (https://at.mouser.com/Search/ProductDetail.aspx?R=BC547CGvirtualkey58410000virtualkey863-BC547CG)
UART1 | CONN_4 | PIN_ARRAY_4x1
UART2 | CONN_4 | PIN_ARRAY_4x1
UART3 | CONN_4 | PIN_ARRAY_4x1
UART4 | CONN_4 | PIN_ARRAY_4x1
UART5 | CONN_4 | PIN_ARRAY_4x1
UART6 | CONN_4 | PIN_ARRAY_4x1

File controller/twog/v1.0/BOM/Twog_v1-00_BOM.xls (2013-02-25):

 | Twog v1.00 Bill Of Material | 2008-04-03
Qty | Manufacturer part # | Schematic part name / value | Designator | Description | Manufacturer(s) | Package | Optional | Farnell.com | Digikey.com | Mouser.com | Other distributor
 | Resistors
2 | MC 0.063W 0603 5% 33R ERJ-3EKF33R0V 301-33-RC | 33 | R21,R22 | 1/16W, 5% | Multicomp Panasonic - ECG Xicon | 0603 |  | 9332006 | P33HCT-ND | 301-33-RC
1 | MC 0.063W 0603 5% 100R ERJ-3EKF1000V 301-100-RC | 100 | R5,R24 | 1/16W, 5% | Multicomp Panasonic - ECG Xicon | 0603 |  | 9331689 | P100HCT-ND | 301-100-RC
1 | MC 0.063W 0603 5% 330R ERJ-3EKF3300V 301-330-RC | 330 | R4 | 1/16W, 5% | Multicomp Panasonic - ECG Xicon | 0603 |  | 9332014 | P330HCT-ND | 301-330-RC
3 | MC 0.063W 0603 5% 1K ERJ-3EKF1001V 301-1.0K-RC | 1K | R16,R17,R23 | 1/16W, 5% | Multicomp Panasonic - ECG Xicon | 0603 |  | 9331697 | P1.00KHCT-ND | 301-1.0K-RC
3 | MC 0.063W 0603 5% 1K5 ERJ-3EKF1501V 301-1.5K-RC | 1.5K | R2,R19,R20 | 1/16W, 5% | Multicomp Panasonic - ECG Xicon | 0603 |  | 9331808 | P1.50KHCT-ND | 301-1.5K-RC
2 | MC 0.063W 0603 5% 1K8 ERJ-3EKF1801V 301-1.8K-RC | 1.8k (see note1) | R13, R18 | 1/16W, 5% | Multicomp Panasonic - ECG Xicon | 0603 |  | 9331867 | P1.8KHCT-ND | 301-1.8K-RC
3 | MC 0.063W 0603 5% 3K3 ERJ-3EKF3301V 301-3.3K-RC | 3.3K | R3,R14,R15 | 1/16W, 5% | Multicomp Panasonic - ECG Xicon | 0603 |  | 9332022 | P3.3KHCT-ND | 301-3.3K-RC
7 | MC 0.063W 0603 5% 10K ERJ-3EKF1002V 301-10K-RC | 10K | R1, R6 to R11 | 1/16W, 5% | Multicomp Panasonic - ECG Xicon | 0603 |  | 9331700 | P10.0KHCT-ND | 301-10K-RC
1 | MC 0.063W 0603 5% 15K ERJ-3EKF1502V 301-15K-RC | 15K (see note2) | R12 | 1/16W, 5% | Multicomp Panasonic - ECG Xicon | 0603 |  | 9331816 | P15.0KHCT-ND | 301-15K-RC
 | Capacitors
4 | C0603C180J5GAC | 18pF | C26 to C29 | 50V, 5% | Kemet | 0603 |  | 1167794 | 399-1052-1-ND | 80-C0603C180J5G
18 | C0603C104K5RAC | 100nF | C2,C3,C5 to C20 | 50V, 10% | Kemet | 0603 |  | 1288255 | 399-5089-1-ND | 80-C0603C104K5R
2 | T520A336M006ATE070 | 33uF/6V | C24,C25 | SMD tantalum capacitor | Kemet | A case (EIA 3216-18) |  | 1108330 | 399-4719-1-ND | 581-TCJA336M6R200
2 | TAJD107K020R | 100uF/20V | C1,C21 | SMD tantalum capacitor | AVX Corporation | D case (EIA 7343-31) |  | 1135058 | 478-1724-1-ND | 581-TAJD107K020R
 | Semiconductors
1 | LM3940IMP-3.3 | LM3940IMP-3.3 | IC3 | 1A low dropout regulator for 5V to 3.3V conversion | National Semicond. | SOT223 |  | 9779280 | LM3940IMP-3.3CT-ND | N/A
1 | TPS2051BDBV | TPS2051B | IC4 | Current Limited Power Distribution Switch | Texas Instruments | SOT23-5 | yes | 1412124 (x3000pcs!) | 296-21265-1-ND | 595-TPS2051BDBVR
1 | LPC2148FBD64 | LPC2148FBD64 | IC5 | Single-chip ARM7 32-bit microcontroller | NXP | LQFP64 |  | N/A | 568-1765-ND | N/A
1 | CD4017BPW CD74HC4017PW | 4017 | IC6 | Decade Counter/Divider with 10 Decoded Outputs | Texas Instruments | TSSOP16 |  | 1407204 (x2000pcs!) 1407402 (x2000pcs!) | 296-14252-1-ND 296-9423-1-ND | 595-CD4017BPWR 595-CD74HC4017PWR
1 | KP-1608MGC APT1608MGC AP1608MGC | KP-1608MGC | LED1 | SMD Chip Green LED Lamp | Kingbright | 0603 |  | 8529825 | 754-1118-1-ND | 604-AP1608MGC
1 | KP-1608SURC APT1608SURCK | KP-1608SURC | LED2 | SMD Chip Red LED Lamp | Kingbright | 0603 | yes | 8529868 | 754-1123-1-ND | 604-APT1608SURCK
1 | KP-1608SYC APT1608SYCK | KP-1608SYC | LED3 | SMD Chip Yellow LED Lamp | Kingbright | 0603 | yes | 8529841 | 754-1124-1-ND | 604-APT1608SYCK
1 | BC807 BC807-40 BC80740MTF | BC807 | T1 | PNP general purpose transistor | NXP NXP Fairchild | SOT23 |  | 1081219 | 568-1629-1-ND | 512-BC80740MTF
 | Modules
1 | PTH08080WAH | PTH_08080W | IC1 | 2.25A Wide-input adjustable switching regulator | Texas Instruments | specific |  | 1470502 | 296-20432-ND | 595-PTH08080WAH
 | Connectors
7 | 53047-0310 | SRV0,SRV4,SRV2,SRV6,IRV,SRV3,SRV7 | J12 to J18 | Picoblade 3 pins 1.25mm straight header | Molex | specific |  | 9732853 | WM1732-ND | 538-53047-0310
1 | 53047-0410 | IRH | J11 | Picoblade 4 pins 1.25mm straight header | Molex | specific |  | 9733060 | WM1733-ND | 538-53047-0410
4 | 53047-0510 | PPM,I2C,ADC2,ADC1 | J4,J6,J8,J10 | Picoblade 5 pins 1.25mm straight header | Molex | specific | J6, J8,J10 | 9732861 | WM1734-ND | 538-53047-0510
3 | 53047-0710 | SPI,CAM,DOWNLOAD/GPS | J3,J5,J7 | Picoblade 7 pins 1.25mm straight header | Molex | specific | J3,J5 | 9732870 | WM1736-ND | 538-53047-0710
2 | 53047-0810 | SERIAL,USB | J2,J9 | Picoblade 8 pins 1.25mm straight header | Molex | specific |  | 1012258 | WM1737-ND | 538-53047-0810
 | Other
1 | 405C35B12M00000 | CTS405 12MHz | Q1 | SMD 12MHz Quartz Crystal | CTS | specific |  | N/A | CTX639CT-ND | N/A
 | Note 1 | R13 calculated according attached ADC5 desired input level : 0 => 3.3v 1.8k => 5v (default) 4.7k => 8v 10k => 13v 15K => 18v
 | Note 2 | R12 calculated according attached ADC6 desired input level : 0 => 3.3v 1.8k => 5v 4.7k => 8v 10k => 13v 15K => 18v (default)
 | Note 3 | For sales make contact with Ublox distributor in the appropriate region (http://www.u-blox.com/disti/index.html)
 |  | This is part of the Paparazzi project (paparazzi.enac.fr). Copyright (C) 2008 ENAC Michel Gorraz See the COPYING file of the project for copying conditions.

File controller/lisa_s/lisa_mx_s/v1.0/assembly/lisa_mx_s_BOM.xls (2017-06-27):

Quantity | Designator | Value | Footprint | Comment | Description | LibRef | farnell
6 | C1, C3, C4, C8, C11, C24 | 4.7uF 16V | V0603 | 0603 | Capacitor | Cap, K0603_100nF_50V_X7R | 2211173
12 | C2, C7, C10, C17, C18, C19, C20, C21, C22, C23, C25, C26 | 100nF 50V | V0402 | 0402 | Capacitor | CAP | 2210822
2 | C5, C12 | 10nF | V0402 | 0402 | Capacitor | Cap | 1414575
1 | C6 | 2.2nF | V0402 | 0402 | Capacitor | CAP | 1828884
3 | C9, C13, C14 | 2.2uF 6V | V0402 | 0402 | Capacitor | Cap | 2118127
2 | C15, C16 | 22pF | V0402 | 0402 | Capacitor | Cap | 2496799
2 | D1, D2 | Led Red 0603 | KP-1608SURC_R | RED | Typical RED, GREEN, YELLOW, AMBER GaAs LED | LED2 | ?
2 | L1, L2 | 10uH | V0402RES | 0402 | FERRITE BEAD, 1OHM, 100MA, 0402 | Res3 | 1669675
8 | R1, R2, R4, R9, R10, R11, R12, R13 | 10k | V0402RES | 0402 | Resistor | Res3 | 9241000
2 | R3, R14 | 1k | V0402RES | 0402 | Resistor | Res3 | 9335757
1 | IC1 | STM32F405RGT6 | LQFP64 | STM32F40x-RG_Dirk |  | STM32F40x-RG_Dirk | 2064363
1 | U1 | MS5611-01BA01 | MS5611-01BA | MS5611-01BA01 or 03 | MS5611-01BA01 High Resolution Barometer Module | MS5611-01BA01 | 2362662
1 | U2 | MPU6000 | mpu60X0 | MPU6000 | INVENSENSE Integrated Dual Axis Gyroscope | MPU6000 | 1862383
1 | U3 | LP2992AIM3.3 | SOT-23-OT5_N | 3.3V LDO | Micropower 250 mA Low-Noise Ultra Low-Dropout Regulator in SOT-23 and LLP Packages | LP2992AIM5-5.0 | 1469141
1 | U4 | VL53L0X | VL53L0Xtra | VL53L0X |  | VL53L0X
1 | Y1 | XTAL, 12.000MHZ, 18PF, SMD, 3.2X2.5 | CFPX-5 | 3SMXB | Surface Mount Quartz Crystal | 3SMXB | 2308709

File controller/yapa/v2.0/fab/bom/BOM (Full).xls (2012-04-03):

Comment | Description | Designator | Footprint | LibRef | Quantity | Supplier 1 | Supplier Part Number 1 | farnell
1k |  | R1, R2, R3, R4, R5, R6, R7, R8, R9, R10, R11, R13, R14, R16, R17, R18, R21, R25, R29, R35 | 0603RES | RES1 | 20
1.5K |  | R23, R26, R33 | 0603RES | RES1 | 3 | Digi-Key
1.8k |  | R27 | 0603RES | RES1 | 1 | Digi-Key
3.3k |  | R30 | 0603RES | RES1 | 1 | Digi-Key
10K |  | R12, R15, R19, R20, R22, R24, R32 | 0603RES | RES1 | 7 | Digi-Key | 541-10.0KLCT-ND
18pF |  | C12, C13, C33, C34 | 0603 | CAP | 4 | Digi-Key | 445-1238-1-ND
33 |  | R28, R31 | 0603RES | RES1 | 2 | Digi-Key | 541-33.0LCT-ND
33uF/6V |  | C23, C29, C41 | T491A | ELECTRO1 | 3 | Digi-Key | 399-4719-1-ND
100nF |  | C6, C7, C8, C9, C10, C11, C14, C15, C16, C17, C18, C19, C20, C21, C24, C25, C26, C28, C31, C32, C35, C36, C37, C39, C42, C43 | 0603 | CAP | 26
100uF/20V |  | C38, C40 | T491D | ELECTRO1 | 2
330 |  | R34 | 0603RES | RES1 | 1 | Digi-Key | 541-330LCT-ND
470nF |  | C22, C27 | 0805 | CAP | 2 |  |  | 1414037
0603 | Capacitor | C1, C2, C3, C4, C5, C30 | 0603 | Cap | 6
4017 |  | U2 | 4017PW | 4017 | 1 | Digi-Key | 296-14252-1-ND
Analog | Header, 6-Pin | Analog | HDR6 | Header 6 | 1
BC807 | PNP general purpose transistor ( GRZ 10/2007 ) | T1 | BC807 | BC807 | 1 | Digi-Key | 568-1629-1-ND
Cam | Header, 4-Pin | S2 | HDR4 | Header 4 | 1
CTS405 12MHz | Crystal 12 Mhz SMD (DMT 06/2007) | Q1 | CTS_405 | CRYSTAL_CTS_405 | 1 | Digi-Key | CTX639CT-ND
Digital | Header, 2-Pin | Aux | HDR2 | Header 2 | 1
Digital | Header, 3-Pin | I2C | HDR3 | Header 3 | 1
GPS | Header, 5-Pin | J1 | HDR5 | Header 5 | 1
Header 3 | Header, 3-Pin | RC1 | HDR3 | Header 3 | 1
KP-1608SURC | Led jaune 0603, Led rouge 0603 (GRZ 10/2007), Led vert 0603 | LED1, LED2, LED3 | KP-1608SURC | KP-1608SURC, KP-1608SURC_1 | 3 | Digi-Key | 754-1123-1-ND
LPC2148FBD64 | Single-chip ARM7 32-bit microcontroller (GRZ 04/2007) | U3 | LPC2148FBD64 | LPC2148FBD64 | 1 | Digi-Key | 568-1765-ND
LT1963AEST-3.3 | Régulateur 3.3v LDO ( GRZ 09/2007) | U4, U5 | LM3940IMP-3.3 | LM3940IMP-3.3 | 2 | Digi-Key | LT1963AEST-3.3#PBF-ND
MAX3221EEAE | ±15kV ESD-Protected, 1µA, 3.0V/5.5V, 250kbps, RS-232 Transceiver with AutoShutdown | U1 | SSOP16 | MAX3221EEAE | 1 |  |  | 9724508
Mini-Usb Connector | Mini USB Connector | USB2 | miniUSB | USB_Host | 1 |  |  | 1125348
P1 | Header, 3-Pin | ADC1 | HDR3 | Header 3 | 1
P2 | Header, 3-Pin | ADC1/2 | HDR3 | Header 3 | 1
PTH_08080W |  | IC1 | PTH_08080W | PTH_08080W | 1 | Digi-Key | 296-20432-ND
rs232 | Header, 4-Pin | RS232 | HDR4 | Header 4 | 1
S0 | Header, 3-Pin | S0 | HDR3 | Header 3 | 1
S1 | Header, 3-Pin | S1 | HDR3 | Header 3 | 1
S3 | Header, 3-Pin | S3 | HDR3 | Header 3 | 1
S4 | Header, 3-Pin | S4 | HDR3 | Header 3 | 1
S5 | Header, 3-Pin | S5 | HDR3 | Header 3 | 1
S6 | Header, 3-Pin | S6 | HDR3 | Header 3 | 1
S7 | Header, 3-Pin | S7 | HDR3 | Header 3 | 1
S8 | Header, 3-Pin | S8 | HDR3 | Header 3 | 1
S9 | Header, 3-Pin | S9 | HDR3 | Header 3 | 1
Spi | Header, 7-Pin | SPI | HDR7 | Header 7 | 1
SUPPLY | Header, 2-Pin | BAT, Switch | HDR1X2 | Header 2 | 2
TPS2051B | Current Limited Power Distribution Switch (GRZ 10/2007) | U6 | TPS2051B | TPS2051B | 1 | Digi-Key | 296-21265-1-ND
XBee Comm Module | Header, 10-Pin, Dual row | XBee | Xbee | Xbee | 1

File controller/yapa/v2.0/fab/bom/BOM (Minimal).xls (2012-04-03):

Comment | Description | Designator | Footprint | LibRef | Quantity | Supplier 1 | Supplier Part Number 1 | farnell
1k |  | R2, R3, R5, R6, R7, R8, R9, R10, R11, R13, R14, R17, R18, R21, R25, R29, R35 | 0603RES | RES1 | 17
1.5K |  | R23, R26, R33 | 0603RES | RES1 | 3 | Digi-Key
1.8k |  | R27 | 0603RES | RES1 | 1 | Digi-Key
3.3k |  | R30 | 0603RES | RES1 | 1 | Digi-Key
10K |  | R12, R15, R19, R20, R22, R24, R32 | 0603RES | RES1 | 7 | Digi-Key | 541-10.0KLCT-ND
18pF |  | C12, C13, C33, C34 | 0603 | CAP | 4 | Digi-Key | 445-1238-1-ND
33 |  | R28, R31 | 0603RES | RES1 | 2 | Digi-Key | 541-33.0LCT-ND
33uF/6V |  | C23 | T491A | ELECTRO1 | 1
100nF |  | C6, C7, C8, C10, C11, C14, C15, C16, C18, C20, C24, C26, C28, C35, C37, C39, C42, C43 | 0603 | CAP | 18
100uF/20V |  | C38, C40 | T491D | ELECTRO1 | 2
330 |  | R34 | 0603RES | RES1 | 1 | Digi-Key | 541-330LCT-ND
470nF |  | C22 | 0805 | CAP | 1 |  |  | 1414037
0603 | Capacitor | C30 | 0603 | Cap | 1
4017 |  | U2 | 4017PW | 4017 | 1 | Digi-Key | 296-14252-1-ND
BC807 | PNP general purpose transistor ( GRZ 10/2007 ) | T1 | BC807 | BC807 | 1 | Digi-Key | 568-1629-1-ND
CTS405 12MHz | Crystal 12 Mhz SMD (DMT 06/2007) | Q1 | CTS_405 | CRYSTAL_CTS_405 | 1 | Digi-Key | CTX639CT-ND
KP-1608SURC | Led jaune 0603 | LED2 | KP-1608SURC | KP-1608SURC_1 | 1 | Digi-Key | 754-1123-1-ND
LPC2148FBD64 | Single-chip ARM7 32-bit microcontroller (GRZ 04/2007) | U3 | LPC2148FBD64 | LPC2148FBD64 | 1 | Digi-Key | 568-1765-ND
LT1963AEST-3.3 | Régulateur 3.3v LDO ( GRZ 09/2007) | U4 | LM3940IMP-3.3 | LM3940IMP-3.3 | 1 | Digi-Key | LT1963AEST-3.3#PBF-ND
PTH_08080W |  | IC1 | PTH_08080W | PTH_08080W | 1 | Digi-Key | 296-20432-ND
minimal: | -no 1/10th inch headers
Cheaper than a TWOG | -no RS232
 | -no aux switch
 | -no modem power supply
 | -no modem headers

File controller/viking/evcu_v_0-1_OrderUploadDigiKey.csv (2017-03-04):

Digi-Key Part No. | Manufacturer Name | Mfr Part No. | Customer Reference | Qty1
74LVC2G17DW-7DICT-ND | Diodes Incorporated | 74LVC2G17DW-7 | REF21 | 12
101-00303-68-1-ND | Amphenol Commercial Products | 101-00303-68 | REF50 | 6
F2871CT-ND | Littelfuse Inc. | 2920L185DR | REF4 | 3
36-2998-ND | Keystone Electronics | 2998 | REF19 | 3
478-9368-1-ND | AVX Corporation | 06031A300J4T2A | REF37 | 6
WM17141CT-ND | Molex | LLC | 473460001 | REF26 | 6
535-9078-1-ND | Abracon LLC | ABLS-25.000MHZ-B2F-T | REF39 | 3
B360B-FDICT-ND | Diodes Incorporated | B360B-13-F | REF22 | 3
BTS3405GCT-ND | Infineon Technologies | BTS3405G | REF23 | 6
568-6240-1-ND | NXP Semiconductors | BZA456A | 115 | REF24 | 6
445-5640-1-ND | TDK Corporation | CGA3E2C0G1H101J080AA | REF7 | 6
445-5659-1-ND | TDK Corporation | CGA3E2X7R1H102K080AA | REF6 | 24
445-5666-1-ND | TDK Corporation | CGA3E2X7R1H104K080AA | REF5 | 129
445-7878-1-ND | TDK Corporation | CGA3E3X5R1H105K080AB | REF35 | 21
H11630CT-ND | Hirose Electric Co Ltd | DF40C-70DP-0.4V(51) | REF48 | 3
P15124CT-ND | Panasonic Electronic Components | ERB-RE1R00V | REF43 | 3
P120HCT-ND | Panasonic Electronic Components | ERJ-3EKF1200V | REF10 | 6
P2.43KHCT-ND | Panasonic Electronic Components | ERJ-3EKF2431V | REF13 | 6
P41.2KHCT-ND | Panasonic Electronic Components | ERJ-3EKF4122V | REF15 | 6
P4.70KHCT-ND | Panasonic Electronic Components | ERJ-3EKF4701V | REF18 | 21
P1.0KGCT-ND | Panasonic Electronic Components | ERJ-3GEYJ102V | REF9 | 24
P10KGCT-ND | Panasonic Electronic Components | ERJ-3GEYJ103V | REF8 | 69
P1.1KGCT-ND | Panasonic Electronic Components | ERJ-3GEYJ112V | REF11 | 18
P2.2KGCT-ND | Panasonic Electronic Components | ERJ-3GEYJ222V | REF12 | 18
P330GCT-ND | Panasonic Electronic Components | ERJ-3GEYJ331V | REF14 | 3
P47GCT-ND | Panasonic Electronic Components | ERJ-3GEYJ470V | REF17 | 3
P470GCT-ND | Panasonic Electronic Components | ERJ-3GEYJ471V | REF16 | 24
587-3818-1-ND | Taiyo Yuden | FBMH1608HL601-TV | REF42 | 3
768-1007-1-ND | FTDI | Future Technology Devices International Ltd | FT232RL-REEL | REF44 | 3
SAM8799-ND | Samtec Inc. | FTSH-105-01-L-DV-K | REF40 | 3
490-12323-1-ND | Murata Electronics North America | GRT188R61E106ME13D | REF34 | 6
490-12333-1-ND | Murata Electronics North America | GRT188R61H225ME13D | REF36 | 6
296-24818-1-ND | Texas Instruments | ISO1050DUBR | REF45 | 6
ISP452CT-ND | Infineon Technologies | ISP452 | REF46 | 6
490-5839-1-ND | Murata Electronics North America | KCM55WR71J226MH01K | REF38 | 6
MMBT3904LT1GOSCT-ND | ON Semiconductor | MMBT3904LT1G | REF25 | 18
811-2195-5-ND | Murata Power Solutions Inc. | OKI-78SR-3.3/1.5-W36-C | REF27 | 3
811-2196-5-ND | Murata Power Solutions Inc. | OKI-78SR-5/1.5-W36-C | REF28 | 3
945-2271-1-ND | Recom Power | R1SE-3.305/H2-R | REF47 | 6
497-6513-1-ND | STMicroelectronics | SMBJ20CA-TR | REF29 | 3
511-1578-1-ND | Rohm Semiconductor | SML-D12M8WT86 | REF49 | 3
296-8747-1-ND | Texas Instruments | SN74AHC1G126DCKR | REF20 | 3
497-11605-ND | STMicroelectronics | STM32F407VGT6 | REF30 | 3
296-23944-1-ND | Texas Instruments | TLV2374QPWRG4Q1 | REF31 | 6
296-24863-1-ND | Texas Instruments | TRS3232EQPWRQ1 | REF32 | 3
296-21527-1-ND | Texas Instruments | TXB0108PWR | REF33 | 9

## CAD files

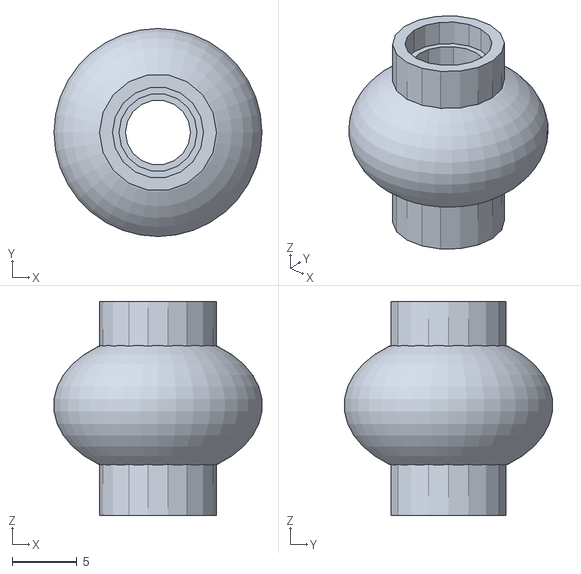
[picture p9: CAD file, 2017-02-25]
3d_print/parrot_bebop2/damper/damper.stl
16.0 x 16.0 x 16.5

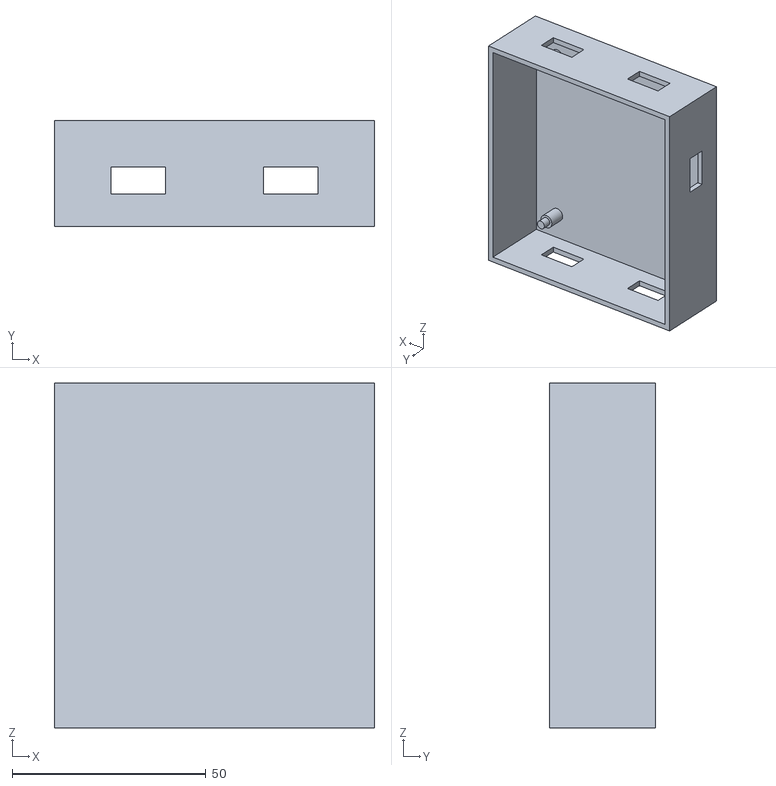
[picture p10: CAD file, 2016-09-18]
controller/lia/breakout_board/box/Lia_Breakout_Box_Bottom.STL
82.7 x 27.4 x 89.1

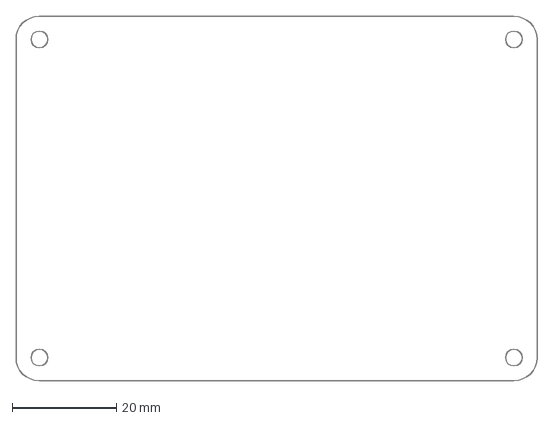
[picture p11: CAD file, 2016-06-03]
controller/stm32f4discovery_daughterboard/V1.0 THT/stm32f4discovery_daughterboard_outline.dxf
100.0 x 70.0 mm

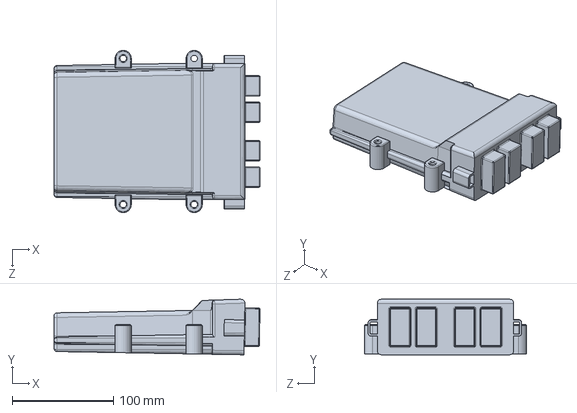
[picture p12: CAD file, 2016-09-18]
controller/viking/3D_models/DEUTSCHBOX.SLDPRT
203.1 x 54.9 x 160.0 mm

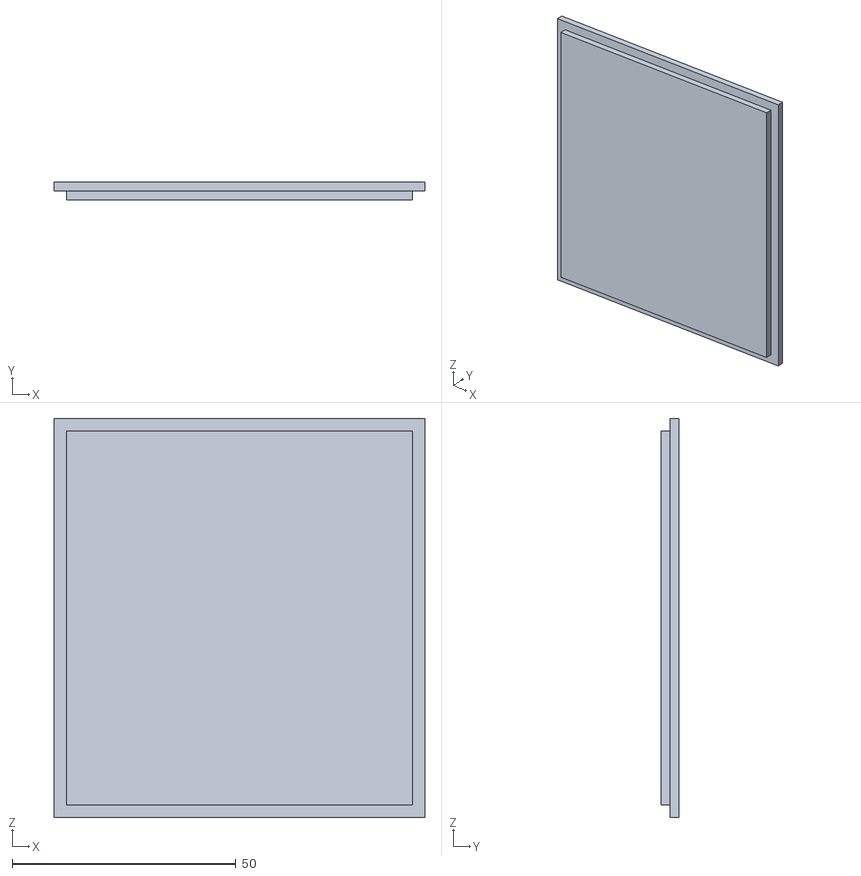
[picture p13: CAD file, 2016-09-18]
controller/lia/breakout_board/box/Lia_Breakout_Box_Top.STL
82.7 x 4.00 x 89.1

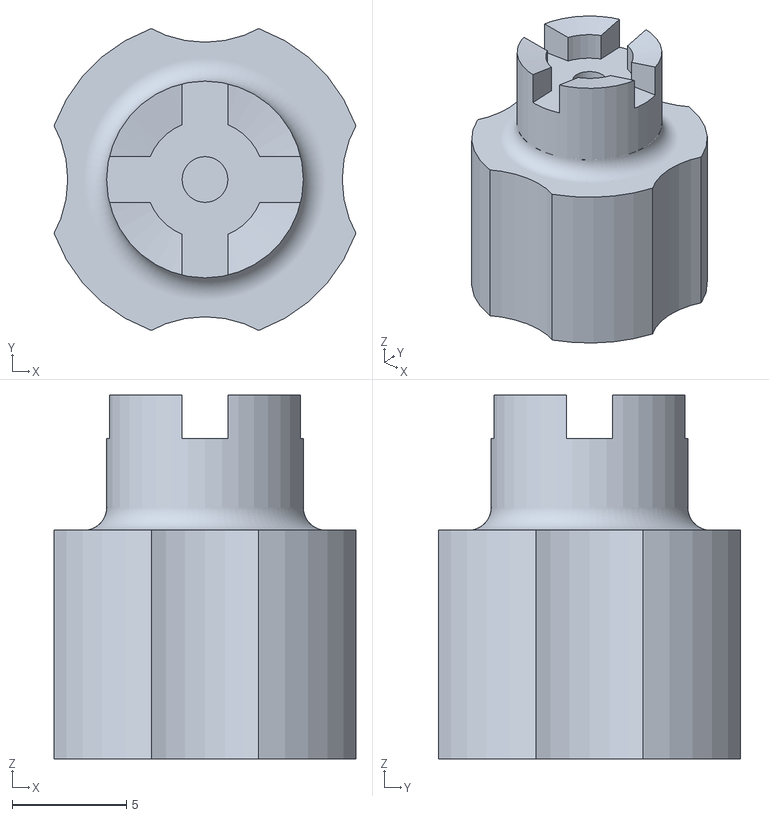
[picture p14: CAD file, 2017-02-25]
3d_print/parrot_bebop2/damper/damper_tool.stl
13.2 x 13.2 x 15.9

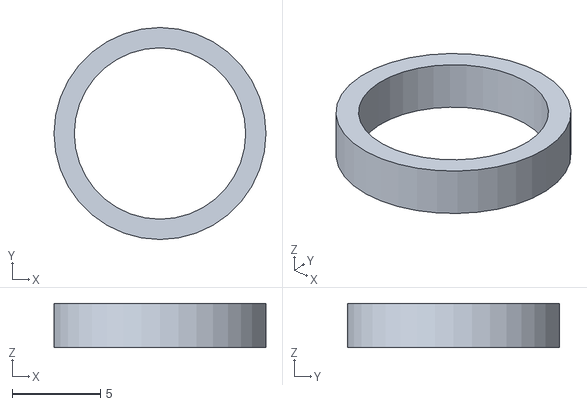
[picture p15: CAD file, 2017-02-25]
3d_print/parrot_bebop2/damper/damper_washer.stl
12.0 x 12.0 x 2.50

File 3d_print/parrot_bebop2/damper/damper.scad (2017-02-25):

difference() {
  union(){
    /* main cylinder */
    cylinder(h=16.5, r=4.5, $fn=18);
    /* main sphere */
    translate([0,0,8.5]) resize(newsize=[16,16,11]) sphere(r=16, $fn=36);
  }
  union(){
    /* lower bore */
    translate([0,0,-1]) cylinder(h=3, r=2.5, $fn=18);
    /* main bore */
    translate([0,0,1]) cylinder(h=16.5, r=3, $fn=18);
    /* upper bore */
    translate([0,0,14.5]) cylinder(h=3, r=3.5, $fn=18);
  }
}

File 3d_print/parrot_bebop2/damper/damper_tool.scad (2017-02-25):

difference() {
  union() {
    cylinder(h=10, r=7, $fn=36);
    translate([0,0,10]) cylinder(h=6, r=4.3, $fn=36);
    translate([0,0,10]) cylinder(h=1, r=5.3, $fn=36);
  }
  union() {
    /* cross */
    translate([0,0,16.5]) cube(size=[2,10,5], center=true);;
    translate([0,0,16.5]) cube(size=[10,2,5], center=true);;
    /* top sphere */
    translate([0,0,45.5]) sphere(r=30, $fn=36);
    /* main bore */
    translate([0,0,14]) cylinder(h=5, r=2.6, $fn=36);
    /* small bore */
    translate([0,0,13]) cylinder(h=5, r=1, $fn=36);
    /* 4x grip */
    translate([11,0,-1]) cylinder(h=12, r=5, $fn=36);
    translate([-11,0,-1]) cylinder(h=12, r=5, $fn=36);
    translate([0,11,-1]) cylinder(h=12, r=5, $fn=36);
    translate([0,-11,-1]) cylinder(h=12, r=5, $fn=36);
    /* adapter */
    translate([0,0,11]) rotate_extrude(convexity=10, $fn = 100)
      translate([5.3, 0, 0])
        circle(r = 1, $fn = 100);      
  }
}

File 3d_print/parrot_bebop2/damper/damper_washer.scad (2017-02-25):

difference() {
  cylinder(h=2.5, r=6, $fn=36);
  translate([0,0,-1]) cylinder(h=4.5, r=4.8, $fn=36);
}

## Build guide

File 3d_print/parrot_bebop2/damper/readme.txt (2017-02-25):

This is a 3D printed new damper to replace the rubber parts that are
originally installed in the Parrot Bebop2. These rubber dampers are too soft
and might cause oscillations with the papareazzi autopilot. I had good
results results printing them in PETG, but PLA might also work. The softer
dampers will give better results for operating the camera.

The wider opening of the damper goes into the metal body of the Bebop2, the
shallow goes to the plastic cross and is secured with the washer.

There is a damper-tool that can be used to fasten the metal screw.

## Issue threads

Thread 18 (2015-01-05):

THT daughterboard

iMattmax, 2015-01-05:
is the THT daughterboard the normal conbfiguration, that work with an normal STM32F4Discovery board or are there some changes in the fw of the F4Discovery?

flixr, 2015-01-05:
Please use the mailing list for questions like this, the issue tracker is not the right place.

Closed 2015-01-05.

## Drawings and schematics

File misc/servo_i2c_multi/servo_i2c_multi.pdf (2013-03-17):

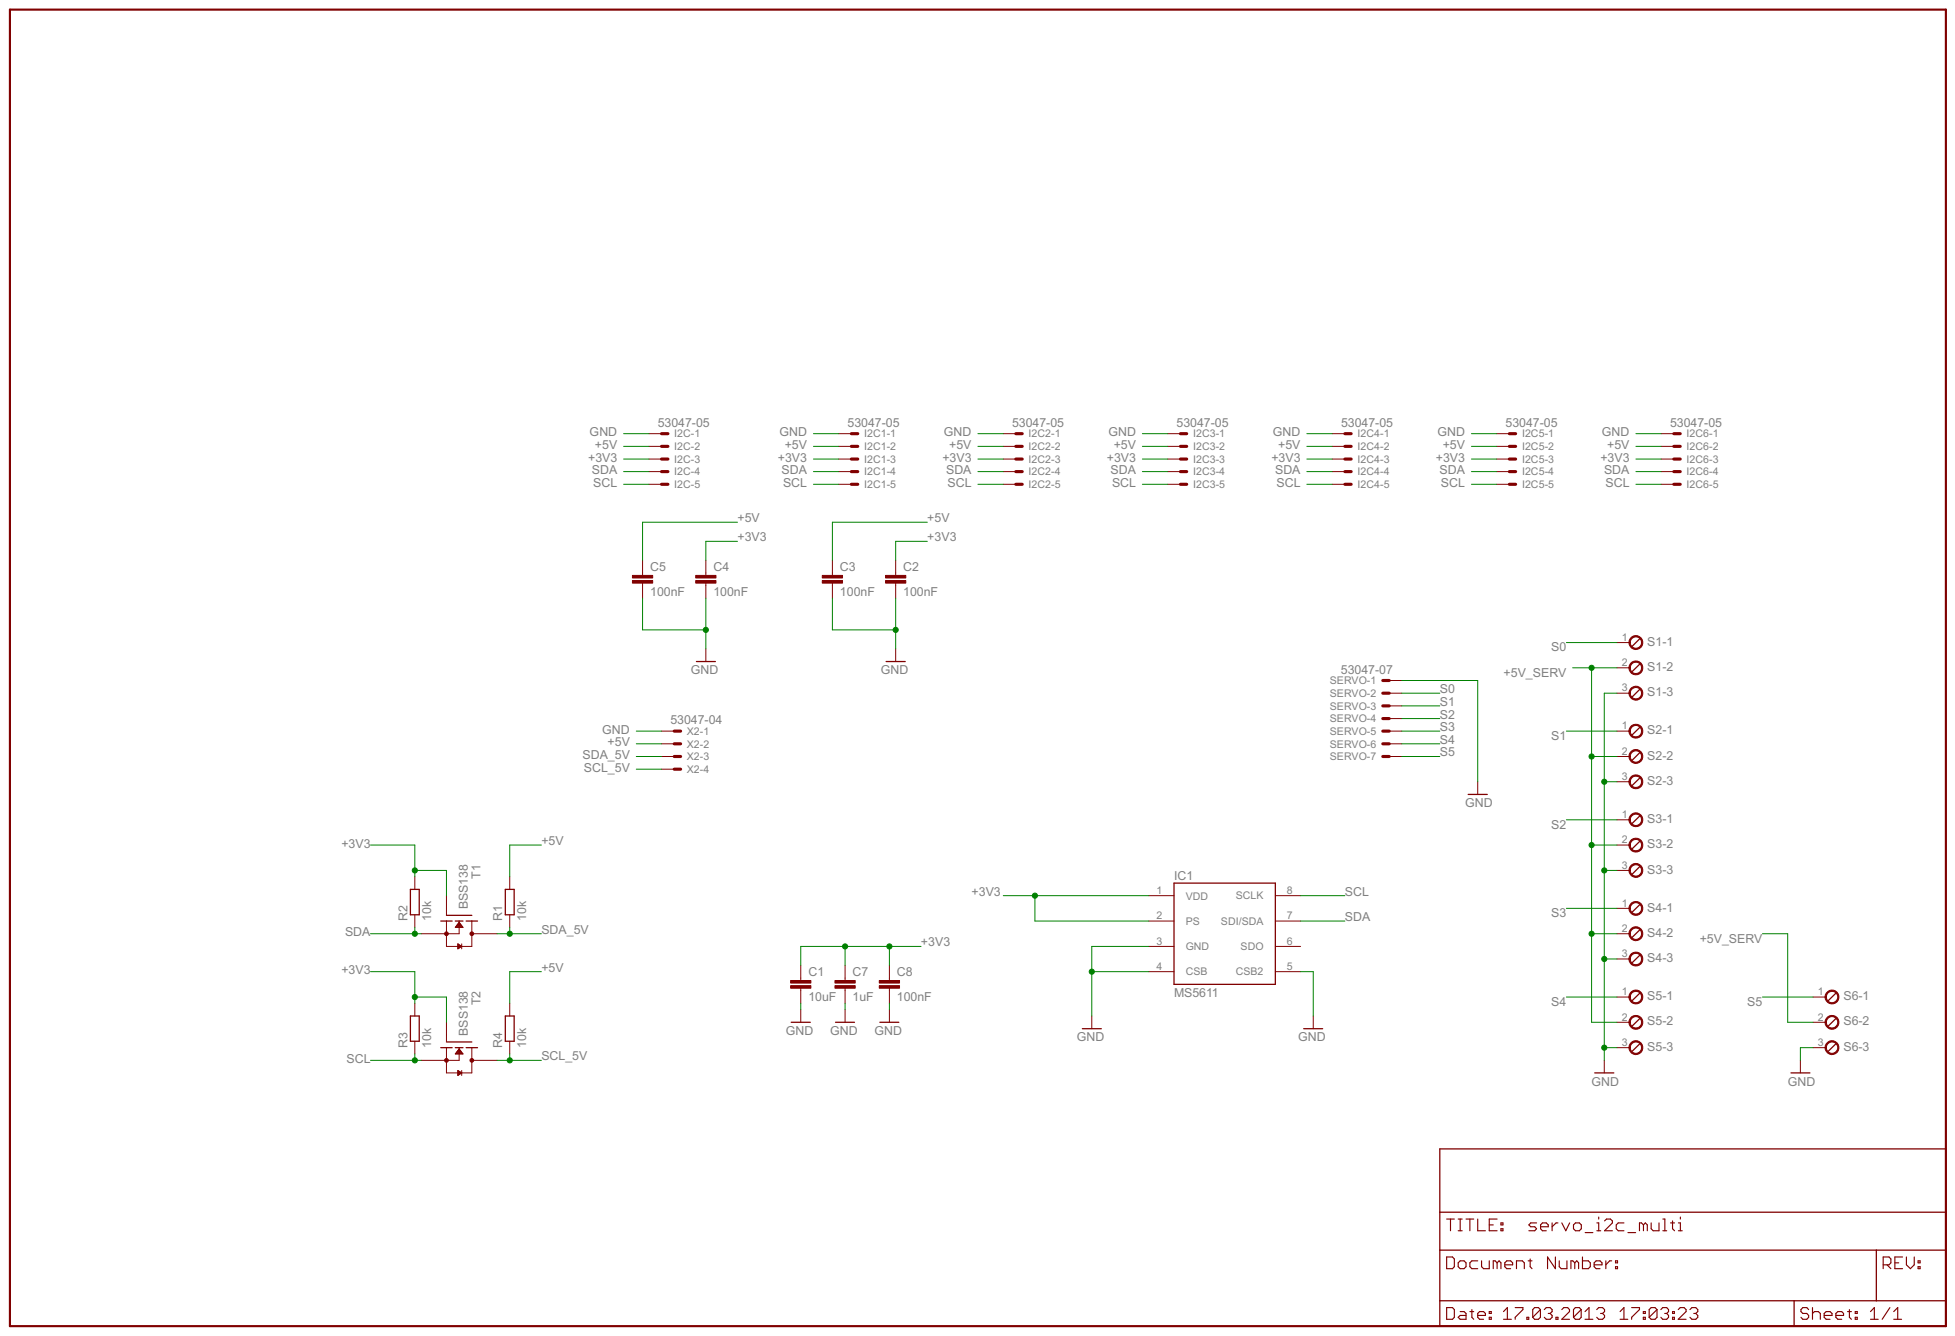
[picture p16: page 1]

SERVO-1 SERVO-2 SERVO-3 SERVO-4 SERVO-5 SERVO-6 SERVO-7

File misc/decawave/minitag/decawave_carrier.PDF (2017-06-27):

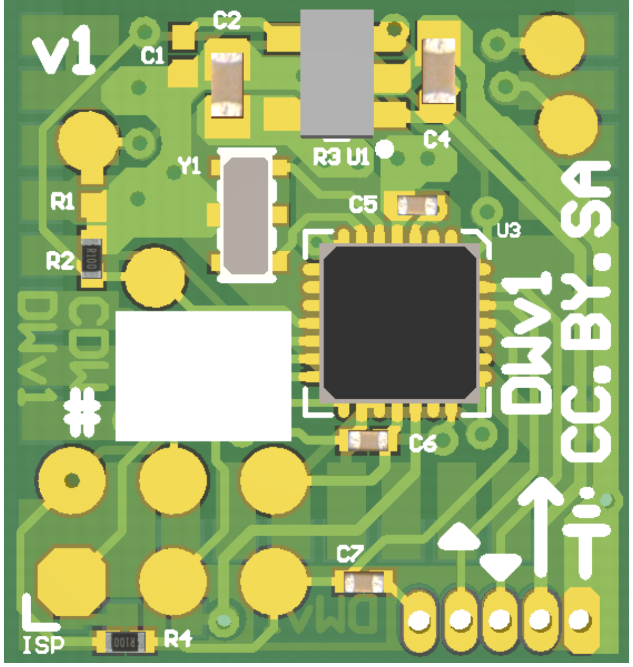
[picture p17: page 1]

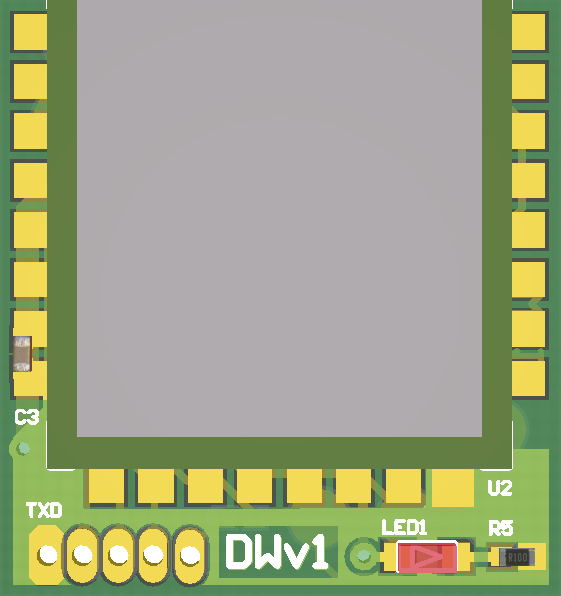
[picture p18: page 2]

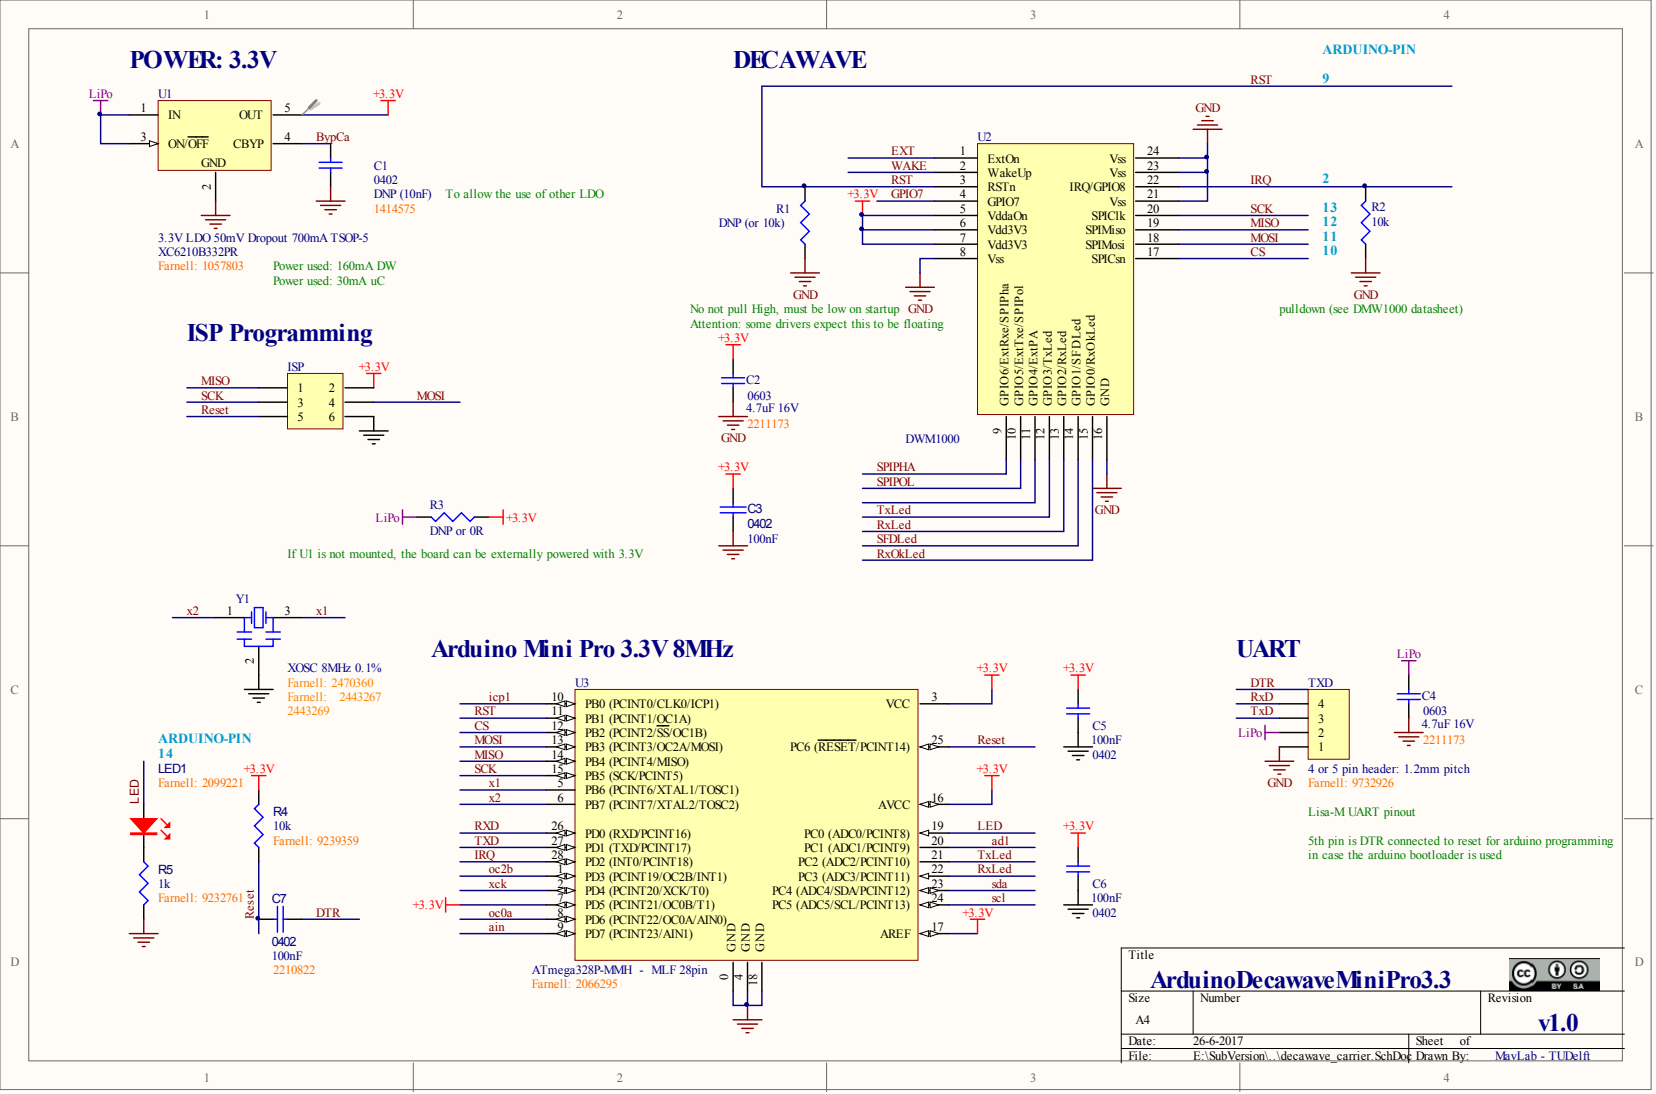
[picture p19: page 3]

GND 16 SPICsn 17 SPIMosi 18 SPIMiso 19 SPIClk 20 Vss 21 IRQ/GPIO8 22 Vss 23 Vss 24

To allow the use of other LDO

GPIO7 4 VddaOn 5

Vdd3V3 6

Attention: some drivers expect this to be floating

If U1 is not mounted, the board can be externally powered with 3.3V

4 or 5 pin header: 1.2mm pitch
Farnell: 9732926

5th pin is DTR connected to reset for arduino programming
in case the arduino bootloader is used

Quantity | Designator | Value | Footprint | Comment | Description | Farnell
2 | C2, C4 | 4.7uF 16V | V0603 | 0603 | Capacitor | 2211173
4 | C3, C5, C6, C7 | 100nF | V0402 | 0402 | Capacitor, CAPACITOR, 100NF, 16V, X7R | 2210822
1 | LED1 | | KP-1608SURC | KP-1608SURC | Led rouge 0603 (GRZ 10/ 2007) | 2099221
2 | R2, R4 | 10k | V0402RES | 10k | Resistor | 9239359, 9241000
1 | R5 | 1k | V0402RES | 1k | | 9232761
1 | U1 | XC6210B332PR | SOT-23-OT5_N | 3.3V LDO 50mV Dropout 700mA | Micropower 250 mA Low-Noise Ultra Low-Dropout Regulator in SOT-23 and LLP Packages | 1057803
1 | U2 | DWM1000 | DWM1000 | DWM1000
1 | U3 | | 28M1 | ATmega328P-MMH - MLF 28pin | 8-Bit AVR Microcontroller with 8K Bytes of In-System Programmable Flash Memory | 2066295
1 | Y1 | | XOSC | XOSC 8MHz 0.1% | Crystal Oscillator | 2470360

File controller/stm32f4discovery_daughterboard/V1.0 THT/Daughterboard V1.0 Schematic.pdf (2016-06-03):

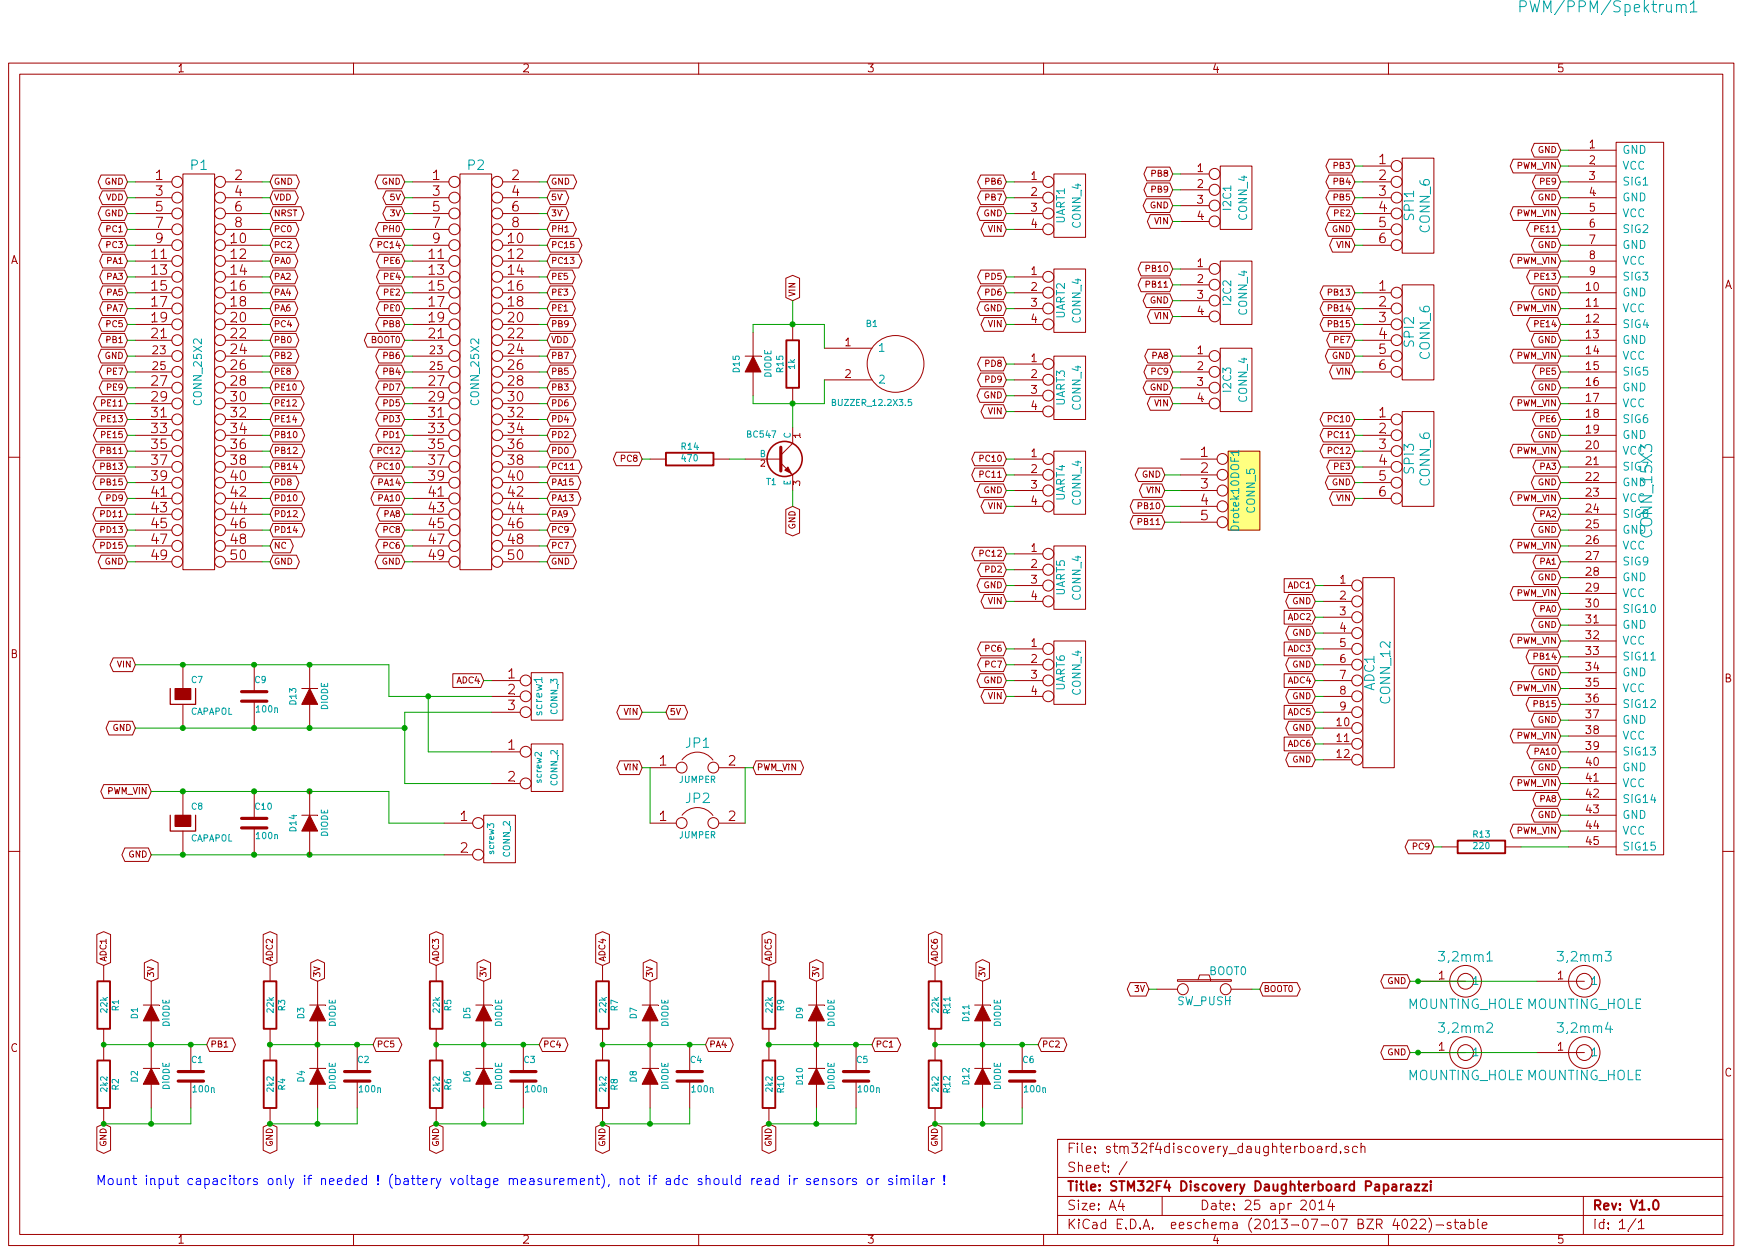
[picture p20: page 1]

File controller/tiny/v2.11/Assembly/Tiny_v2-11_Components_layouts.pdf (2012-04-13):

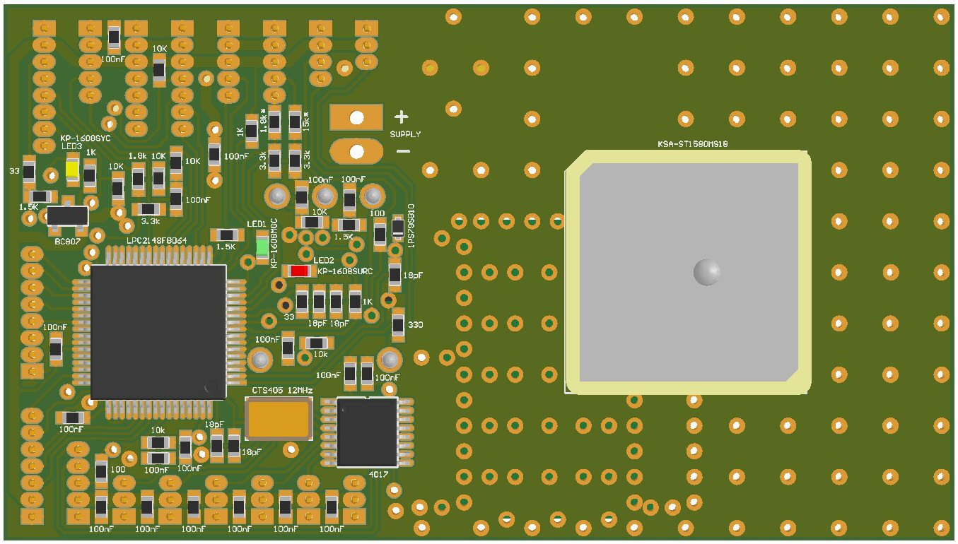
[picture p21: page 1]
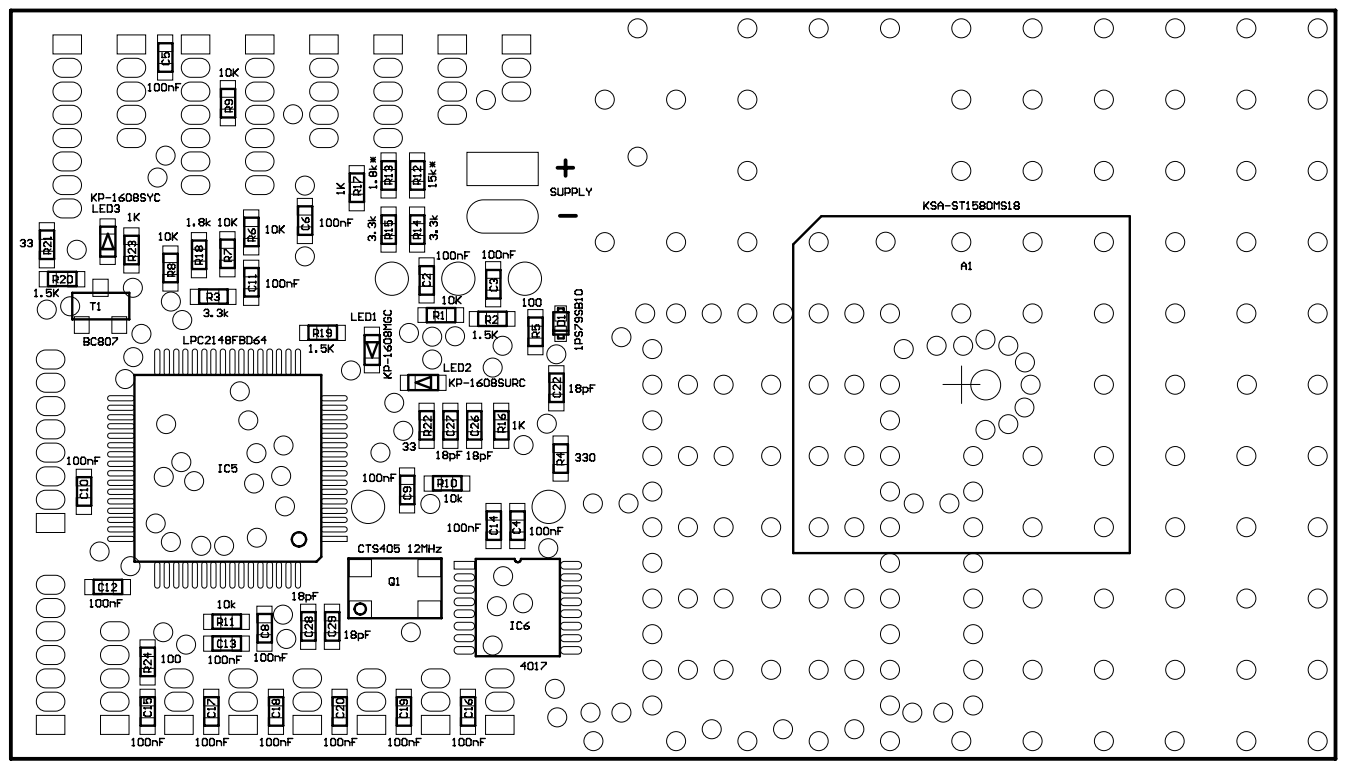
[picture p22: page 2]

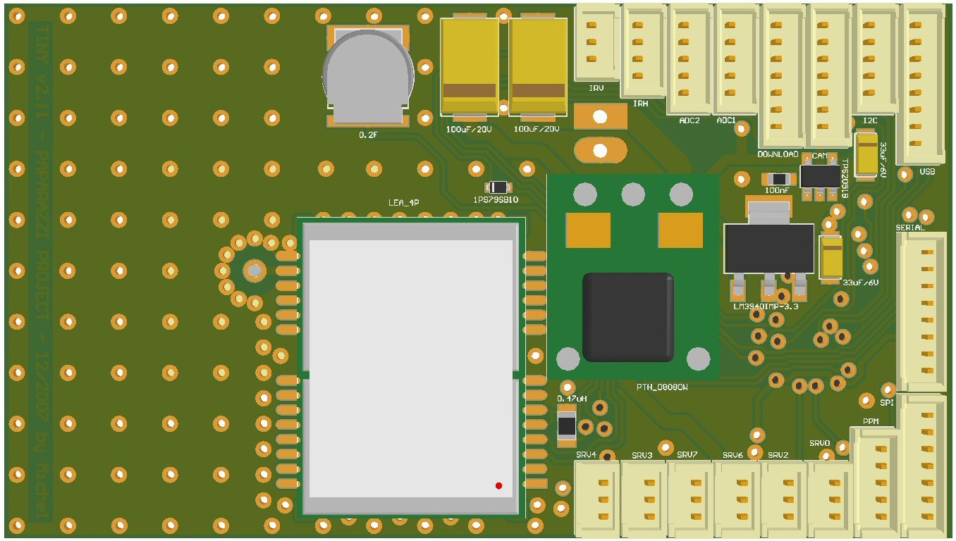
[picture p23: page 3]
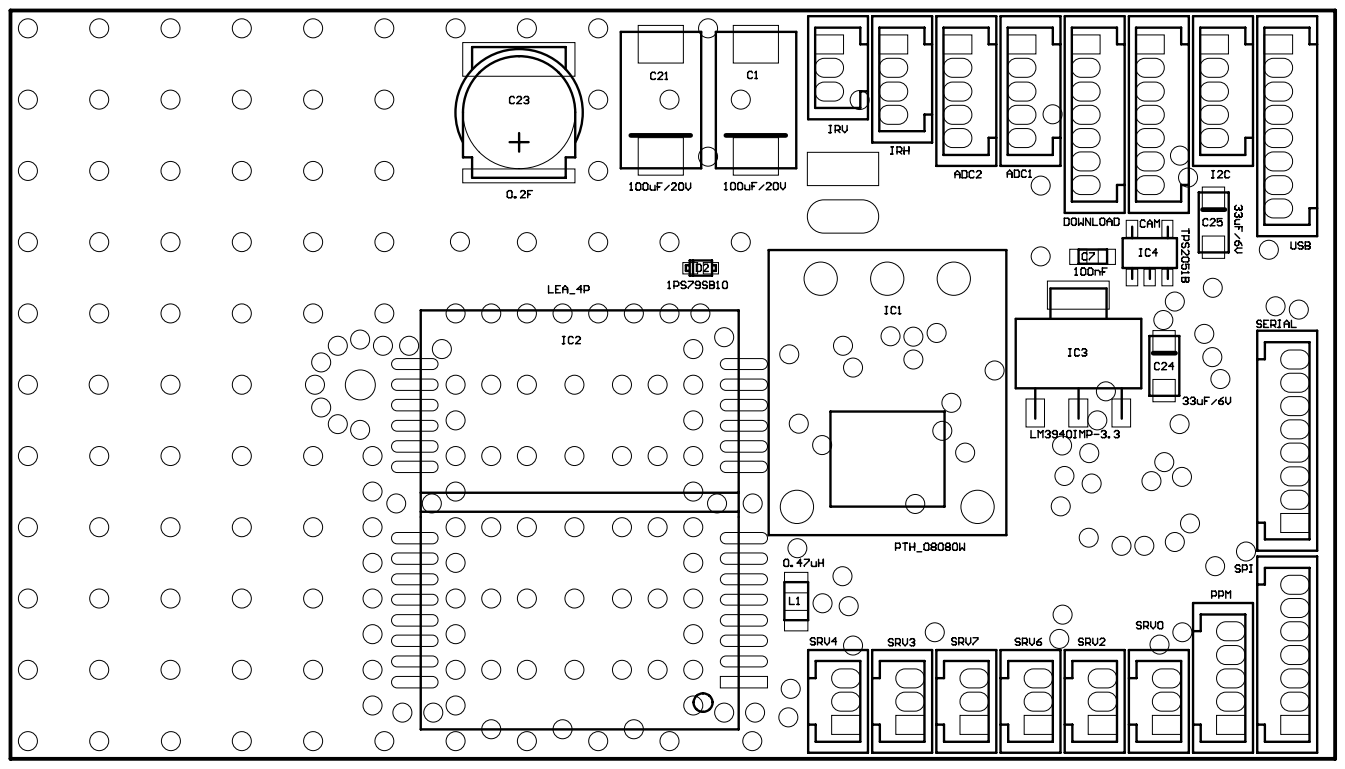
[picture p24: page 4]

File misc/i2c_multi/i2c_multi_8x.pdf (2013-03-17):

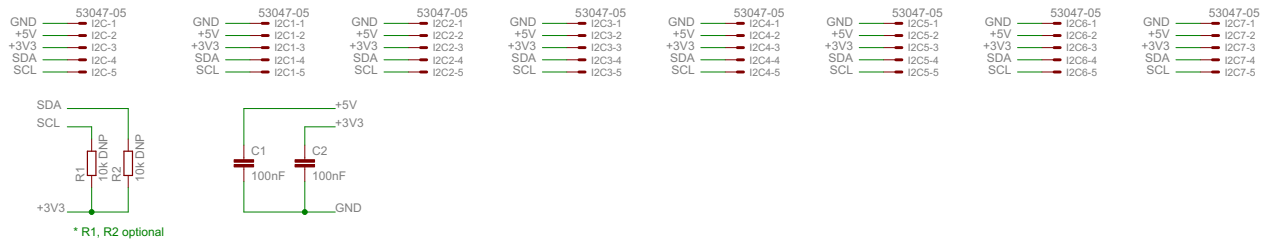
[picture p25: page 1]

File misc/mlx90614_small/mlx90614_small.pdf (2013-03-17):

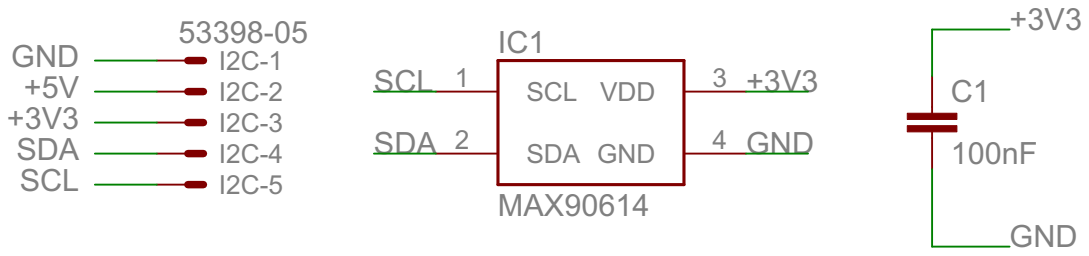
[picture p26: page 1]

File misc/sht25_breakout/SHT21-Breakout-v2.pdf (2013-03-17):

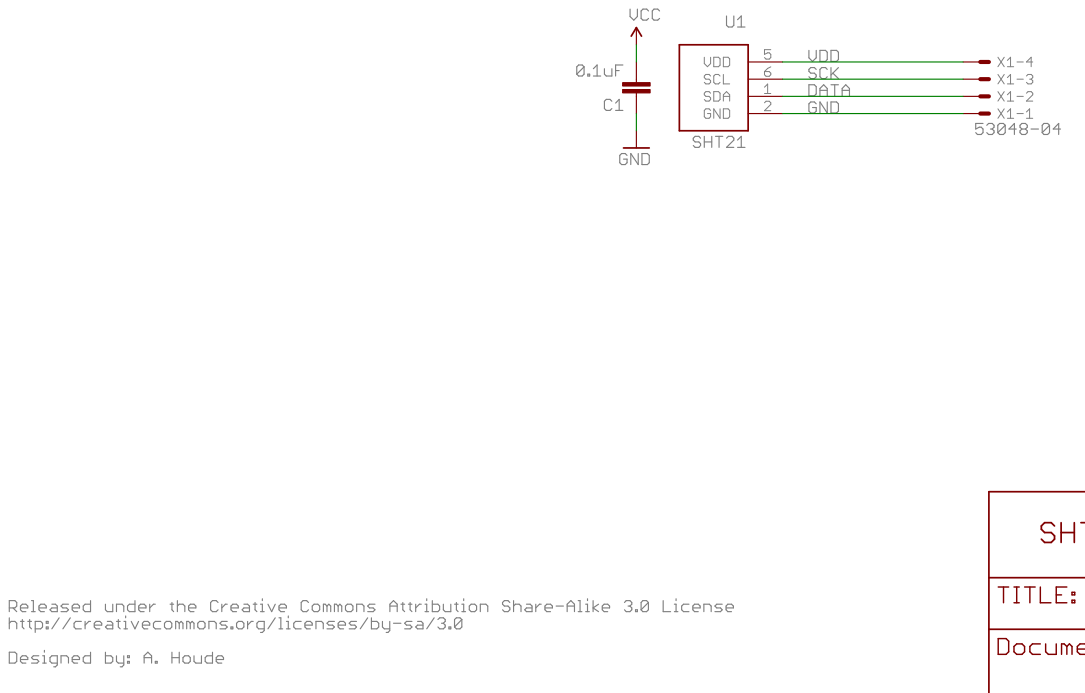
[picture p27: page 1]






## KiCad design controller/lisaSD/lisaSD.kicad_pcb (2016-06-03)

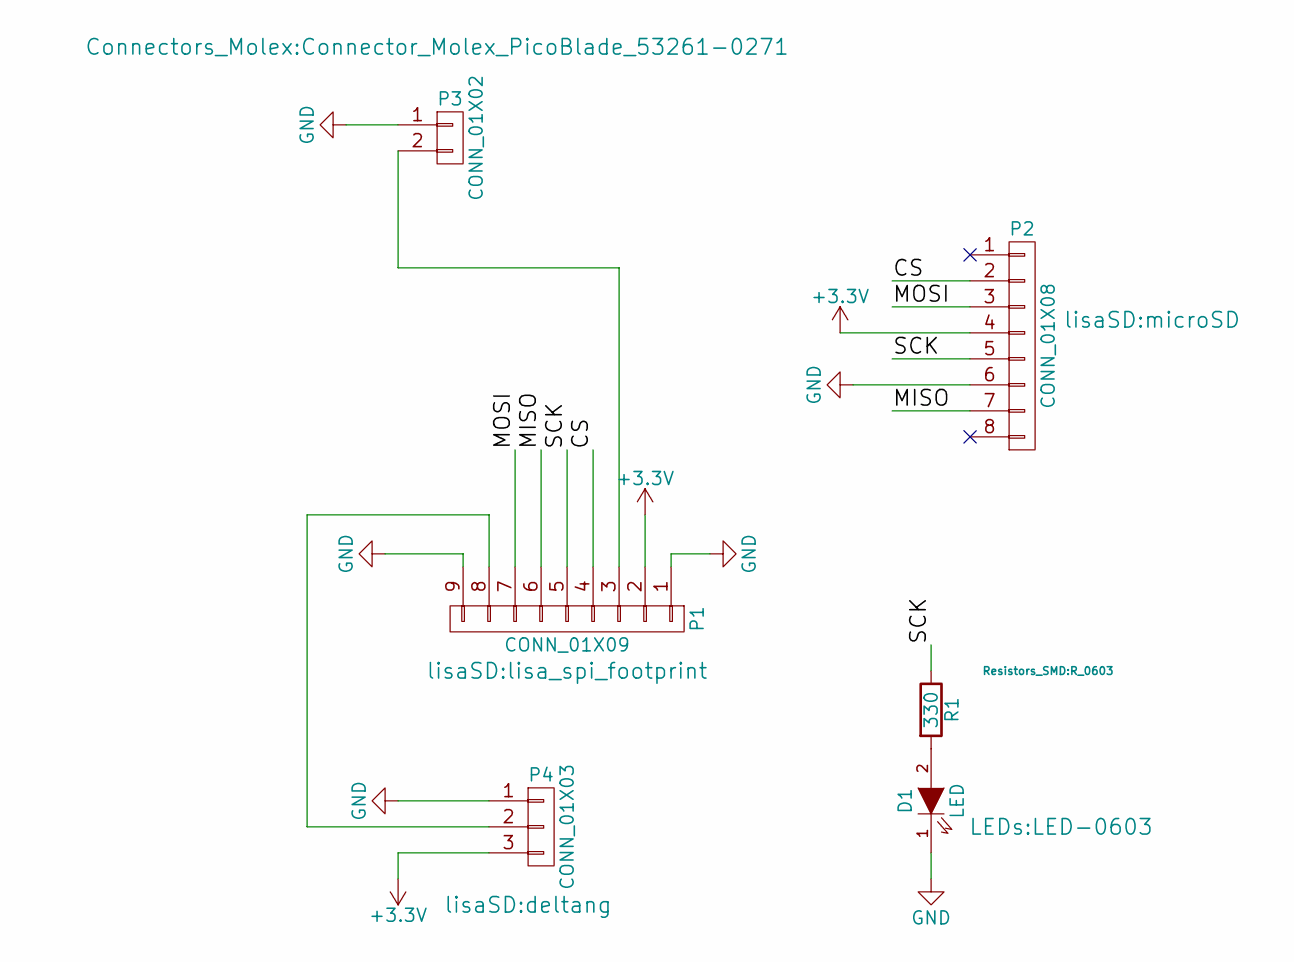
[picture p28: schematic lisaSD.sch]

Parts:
D1: LED; LED-0603
P1: CONN_01X09; lisa_spi_footprint
P2: CONN_01X08; microSD
P3: CONN_01X02; Connector_Molex_PicoBlade_53261-0271
P4: CONN_01X03; deltang
R1: 330; R_0603

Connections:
+3V3: P1.2, P2.4, P4.3
/CS: P1.4, P2.2
/MISO: P1.6, P2.7
/MOSI: P1.7, P2.3
/SCK: P1.5, P2.5, R1.1
GND: D1.1 (K), P1.1, P1.9, P2.6, P3.1, P4.1
unnamed: D1.2 (A), R1.2
unnamed: P1.3, P3.2
unnamed: P1.8, P4.2

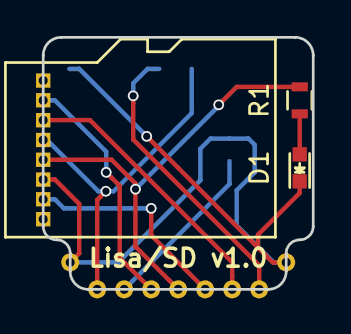
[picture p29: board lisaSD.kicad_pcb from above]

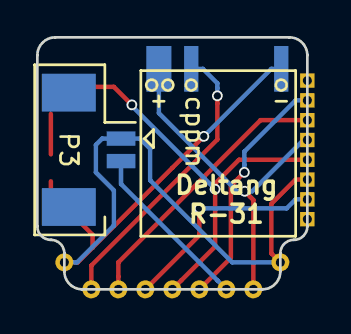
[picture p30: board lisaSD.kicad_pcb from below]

Board: 2 copper layers, 15.0 x 14.0 mm, 6 parts (2 on the bottom side), 9 nets.

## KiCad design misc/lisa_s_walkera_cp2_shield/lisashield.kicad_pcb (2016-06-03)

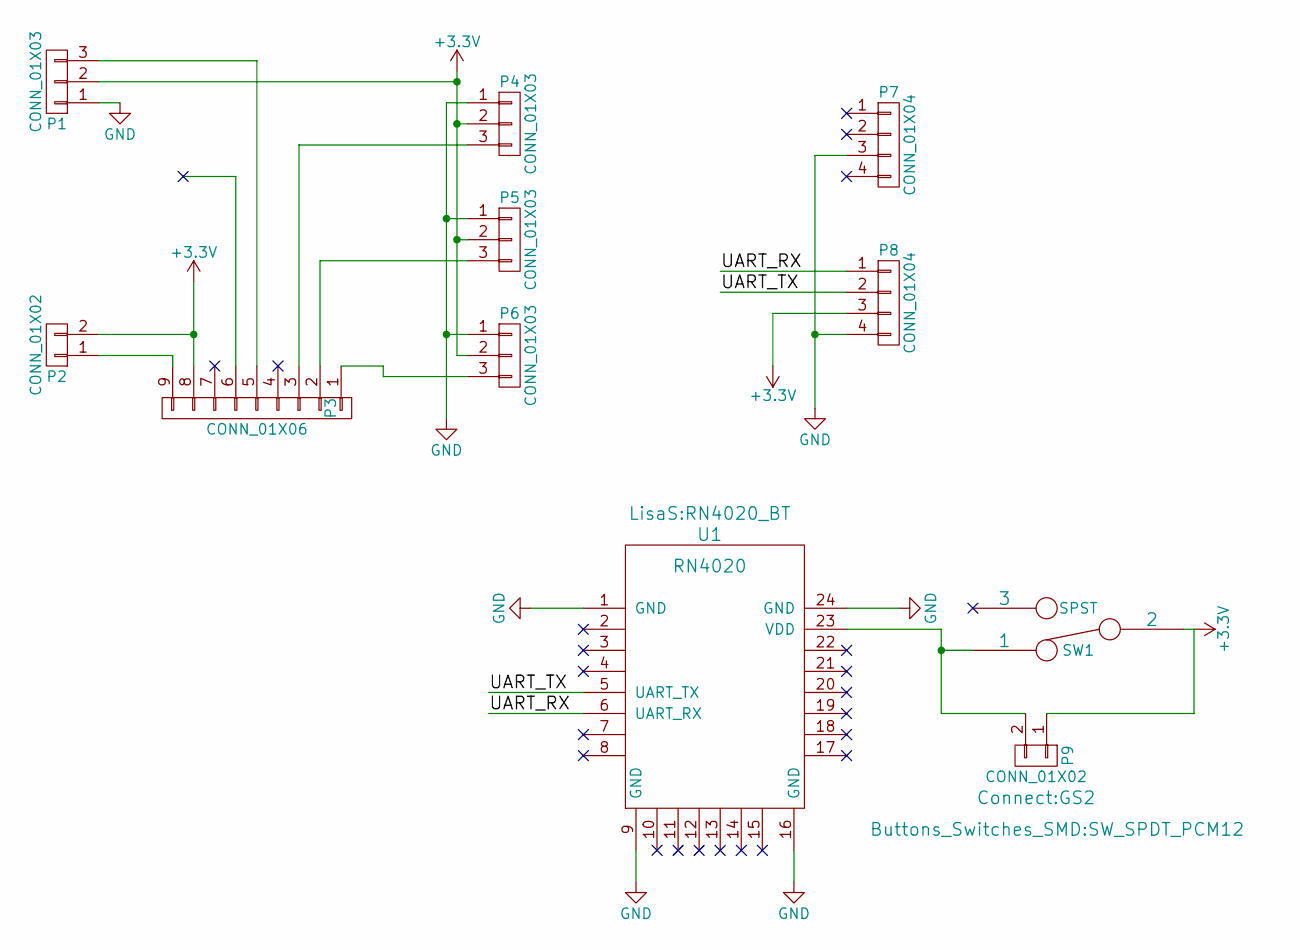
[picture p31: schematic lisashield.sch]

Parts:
P1, P4, P5, P6: CONN_01X03; Connector_Molex_PicoBlade_53047-0310
P2: CONN_01X02; Connector_Molex_PicoBlade_53047-0210
P3: CONN_01X06; 9x1_1.27mm
P7, P8: CONN_01X04; 4x1_1.27mm
P9: CONN_01X02; GS2
SW1: SPST; SW_SPDT_PCM12
U1: RN4020; RN4020_BT

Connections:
+3V3: P1.2, P2.2, P3.8, P4.2, P5.2, P6.2, P8.3, P9.1, SW1.2
/UART_RX: P8.1, U1.6 (UART_RX)
/UART_TX: P8.2, U1.5 (UART_TX)
GND: P1.1, P4.1, P5.1, P6.1, P7.3, P8.4, U1.1 (GND), U1.9 (GND), U1.16 (GND), U1.24 (GND)
unnamed: P1.3, P3.5
unnamed: P2.1, P3.9
unnamed: P3.1, P6.3
unnamed: P3.2, P5.3
unnamed: P3.3, P4.3
unnamed: P9.2, SW1.1, U1.23 (VDD)

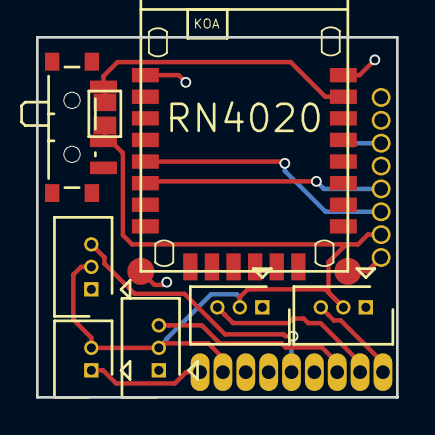
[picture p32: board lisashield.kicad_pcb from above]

Board: 2 copper layers, 20.0 x 20.0 mm, 11 parts (0 on the bottom side), 10 nets.

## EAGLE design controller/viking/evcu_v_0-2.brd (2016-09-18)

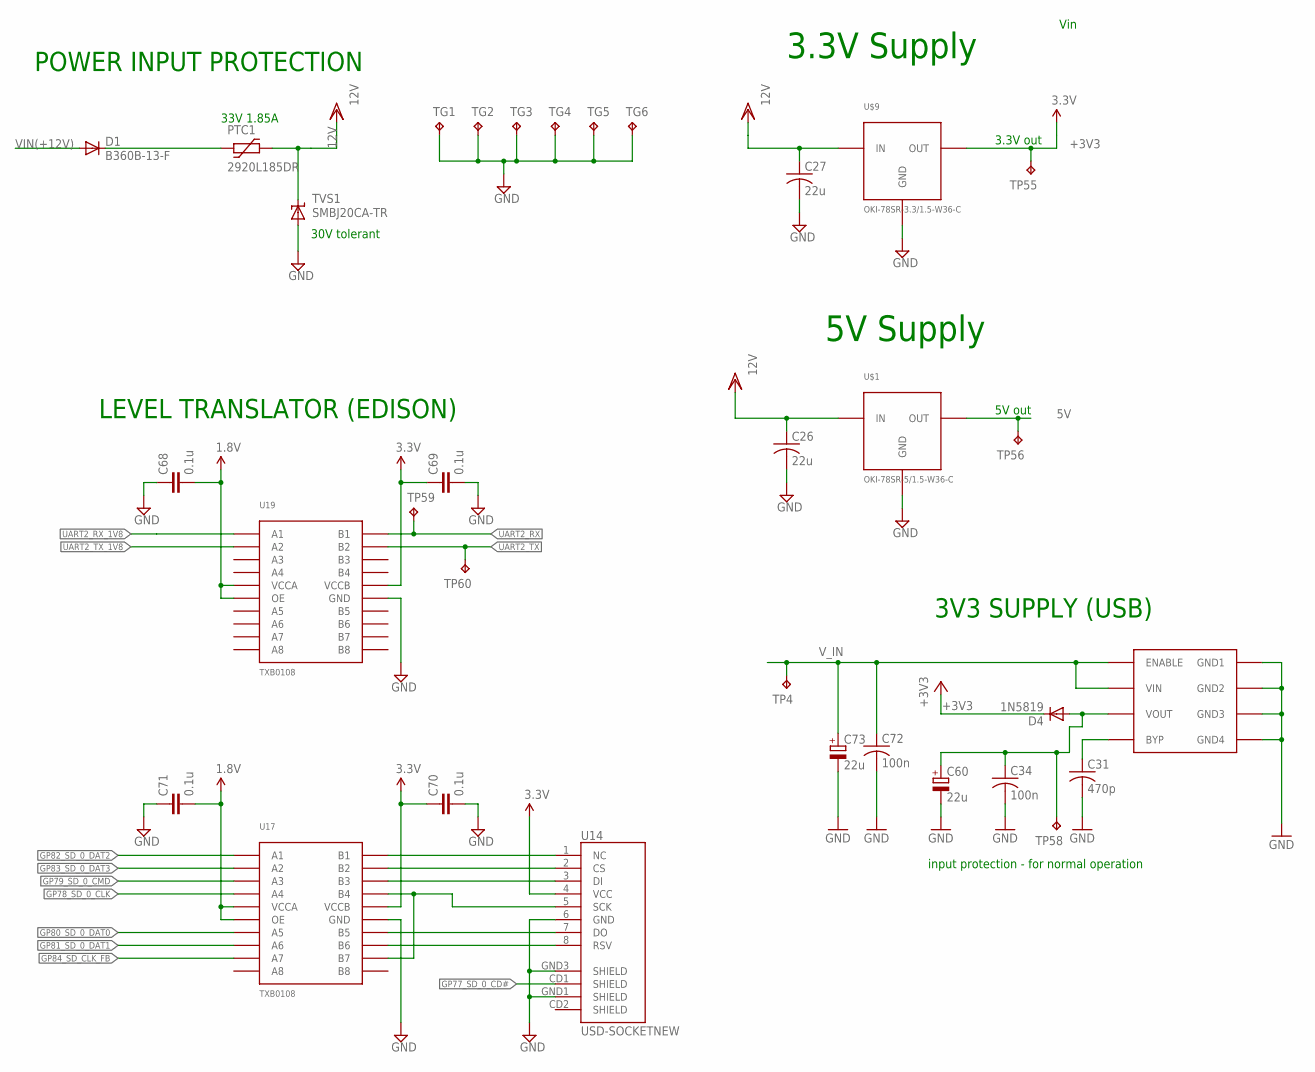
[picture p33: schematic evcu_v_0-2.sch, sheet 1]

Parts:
C26, C27: 22u; C1206
C31: 470p; C0603; PARTNO CC0402KRX7R9BB471
C34: 100n; C0603; PARTNO C0603C104K5RACTU
C60, C73: 22u; 3528/B; PARTNO T491B226M016AT
C68, C69, C70, C71: 0.1u; C0603@1
C72: 100n; C0603; PARTNO LMK105BJ104KV-F
D1: B360B-13-F; SMB
D4: 1N5819; MICROMELF-R; PARTNO RB160SS-40T2R
PTC1: 2920L185DR; 2920L
TG1, TG2, TG3, TG4, TG5, TG6: TPB1,27; B1,27
TP4, TP55, TP56, TP58, TP59, TP60: TPB1,27; B1,27
TVS1: SMBJ20CA-TR; SMBJ; PARTNO SM30T35AY
U14: USD-SOCKETNEW; MICRO-SD-SOCKET-PP
U17, U19: TXB0108; TSSOP20
U$1: OKI-78SR-5/1.5-W36-C; OKI-78SR
U$9: OKI-78SR-3.3/1.5-W36-C; OKI-78SR
VREG1: MIC5209; SOIC8; PARTNO MIC5209-3.3YM

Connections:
5V: TP56.TP, U$1.P3 (OUT); also elsewhere on the board
12V: C26.1, C27.1, PTC1.P$2 (2), TVS1.C, U$1.P1 (IN), U$9.P1 (IN); also elsewhere on the board
+1V8: C68.2, C71.2, U17.2 (VCCA), U17.10 (OE), U19.2 (VCCA), U19.10 (OE); also elsewhere on the board
+3V3: C69.1, C70.1, D4.C, TP55.TP, U14.4 (VCC), U17.19 (VCCB), U19.19 (VCCB), U$9.P3 (OUT); also elsewhere on the board
GND: C26.2, C27.2, C31.2, C34.2, C60.-, C68.1, C69.2, C70.2, C71.1, C72.2, C73.-, TG1.TP, TG2.TP, TG3.TP, TG4.TP, TG5.TP, TG6.TP, TVS1.A, U14.6 (GND), U14.GND1 (SHIELD), U14.GND3 (SHIELD), U17.11 (GND), U19.11 (GND), U$1.P2 (GND), U$9.P2 (GND), VREG1.5 (GND4), VREG1.6 (GND3), VREG1.7 (GND2), VREG1.8 (GND1); also elsewhere on the board
GP77_SD_0_CD#: U14.CD1 (SHIELD); also elsewhere on the board
GP78_SD_0_CLK: U17.5 (A4); also elsewhere on the board
GP79_SD_0_CMD: U17.4 (A3); also elsewhere on the board
GP80_SD_0_DAT0: U17.6 (A5); also elsewhere on the board
GP81_SD_0_DAT1: U17.7 (A6); also elsewhere on the board
GP82_SD_0_DAT2: U17.1 (A1); also elsewhere on the board
GP83_SD_0_DAT3: U17.3 (A2); also elsewhere on the board
GP84_SD_CLK_FB: U17.8 (A7); also elsewhere on the board
unnamed: U14.1 (NC), U17.20 (B1)
unnamed: U14.2 (CS), U17.18 (B2)
unnamed: U14.3 (DI), U17.17 (B3)
unnamed: U14.7 (DO), U17.15 (B5)
unnamed: U14.8 (RSV), U17.14 (B6)
unnamed: C31.1, VREG1.4 (BYP)
unnamed: C34.1, C60.+, D4.A, TP58.TP, VREG1.3 (VOUT)
unnamed: D1.C, PTC1.P$1 (1)
SCK: U14.5 (SCK), U17.13 (B7), U17.16 (B4)
UART2_RX: TP59.TP, U19.20 (B1); also elsewhere on the board
UART2_RX_1V8: U19.1 (A1); also elsewhere on the board
UART2_TX: TP60.TP, U19.18 (B2); also elsewhere on the board
UART2_TX_1V8: U19.3 (A2); also elsewhere on the board
VIN(+12V): D1.A; also elsewhere on the board
V_IN: C72.1, C73.+, TP4.TP, VREG1.1 (ENABLE), VREG1.2 (VIN); also elsewhere on the board

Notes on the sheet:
POWER INPUT PROTECTION
30V tolerant
3.3V out
Vin
3.3V Supply
5V out
5V Supply
33V 1.85A
LEVEL TRANSLATOR (EDISON)
3V3 SUPPLY (USB)
input protection - for normal operation

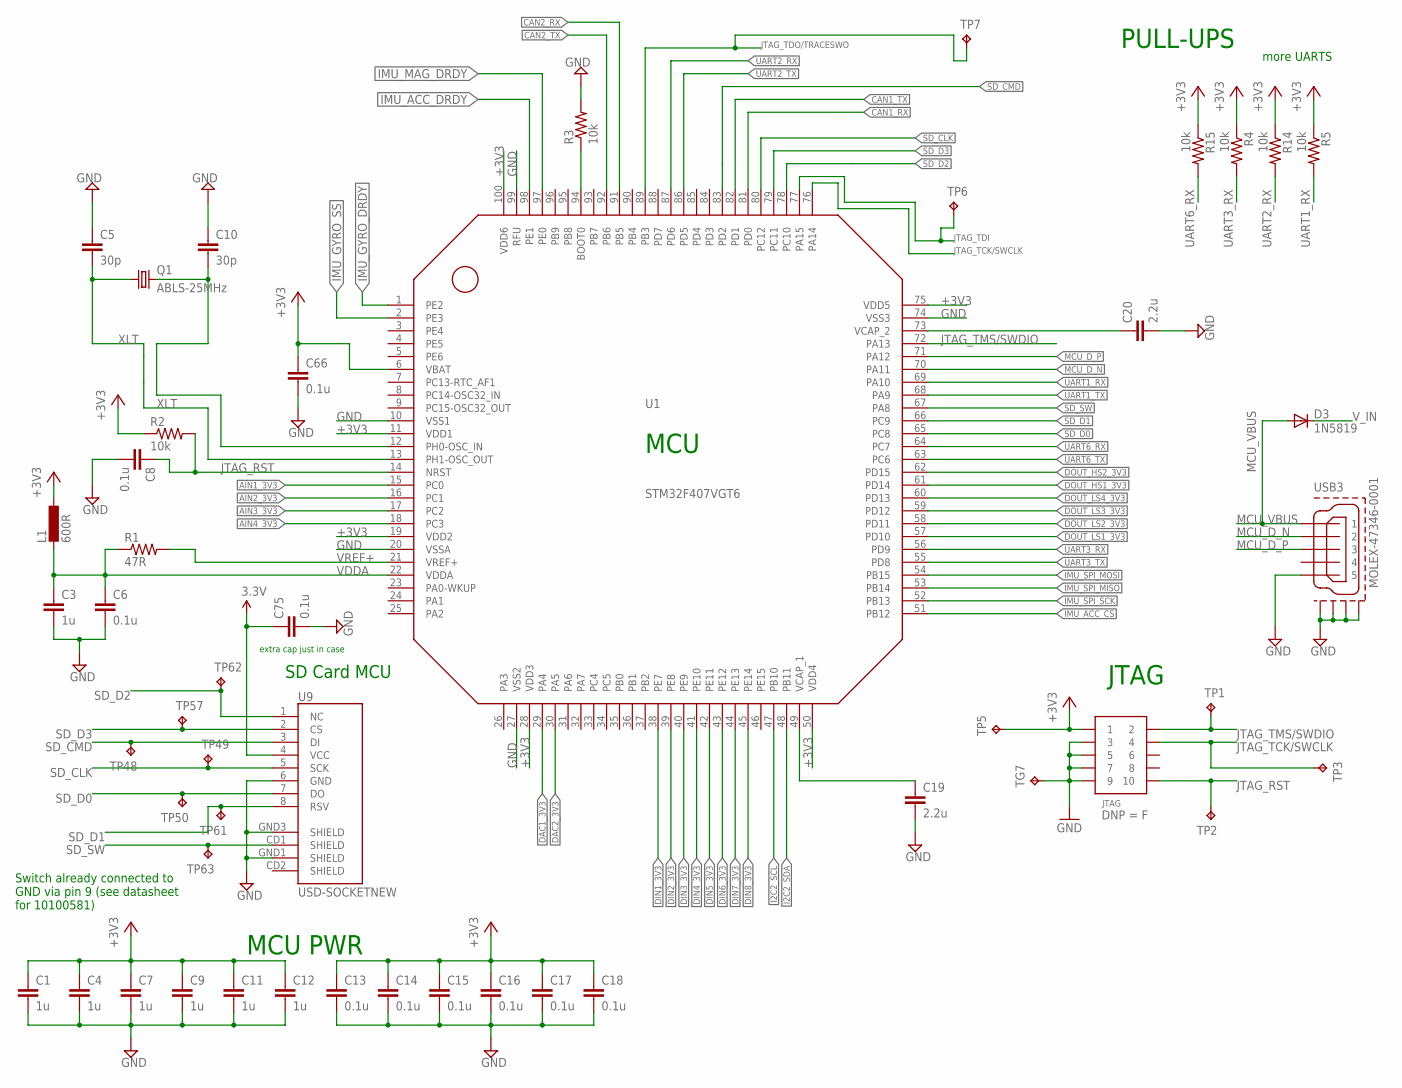
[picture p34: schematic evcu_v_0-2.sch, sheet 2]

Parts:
C1, C3, C4, C7, C9, C11, C12: 1u; C0603@1
C5, C10: 30p; C0603@1
C6, C8, C13, C14, C15, C16, C17, C18, C66, C75: 0.1u; C0603@1
C19, C20: 2.2u; C0603@1
D3: 1N5819; MICROMELF-R; PARTNO RB160SS-40T2R
JTAG: PIN_HDR_EDG_1.27MM_5-2; FTSH-105-DV; PARTNO conn-smd-0.05in-5-2
L1: 600R; 0603-IND
Q1: ABLS-25MHz; CSM-7X-DU
R1: 47R; R0603
R2, R3, R4, R5, R14, R15: 10k; R0603
TG7: TPB1,27; B1,27
TP1, TP2, TP3, TP5, TP6, TP7, TP48, TP49, TP50, TP57, TP61, TP62, TP63: TPB1,27; B1,27
U1: STM32F407VGT6; LQFP100
U9: USD-SOCKETNEW; MICRO-SD-SOCKET-PP
USB3: MOLEX-47346-0001; MOLEX-47364-0001

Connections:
+3V3: C1.1, C4.1, C7.1, C9.1, C11.1, C12.1, C13.1, C14.1, C15.1, C16.1, C17.1, C18.1, C66.1, C75.1, JTAG.1, L1.P$1 (1), R2.1, R4.1, R5.1, R14.1, R15.1, TP5.TP, U1.6 (VBAT), U1.11 (VDD1), U1.19 (VDD2), U1.28 (VDD3), U1.50 (VDD4), U1.75 (VDD5), U1.100 (VDD6), U9.4 (VCC); also elsewhere on the board
AIN1_3V3: U1.15 (PC0); also elsewhere on the board
AIN2_3V3: U1.16 (PC1); also elsewhere on the board
AIN3_3V3: U1.17 (PC2); also elsewhere on the board
AIN4_3V3: U1.18 (PC3); also elsewhere on the board
CAN1_RX: U1.81 (PD0); also elsewhere on the board
CAN1_TX: U1.82 (PD1); also elsewhere on the board
CAN2_RX: U1.91 (PB5); also elsewhere on the board
CAN2_TX: U1.92 (PB6); also elsewhere on the board
DAC1_3V3: U1.29 (PA4); also elsewhere on the board
DAC2_3V3: U1.30 (PA5); also elsewhere on the board
DIN1_3V3: U1.38 (PE7); also elsewhere on the board
DIN2_3V3: U1.39 (PE8); also elsewhere on the board
DIN3_3V3: U1.40 (PE9); also elsewhere on the board
DIN4_3V3: U1.41 (PE10); also elsewhere on the board
DIN5_3V3: U1.42 (PE11); also elsewhere on the board
DIN6_3V3: U1.43 (PE12); also elsewhere on the board
DIN7_3V3: U1.44 (PE13); also elsewhere on the board
DIN8_3V3: U1.45 (PE14); also elsewhere on the board
DOUT_HS1_3V3: U1.61 (PD14); also elsewhere on the board
DOUT_HS2_3V3: U1.62 (PD15); also elsewhere on the board
DOUT_LS1_3V3: U1.57 (PD10); also elsewhere on the board
DOUT_LS2_3V3: U1.58 (PD11); also elsewhere on the board
DOUT_LS3_3V3: U1.59 (PD12); also elsewhere on the board
DOUT_LS4_3V3: U1.60 (PD13); also elsewhere on the board
GND: C1.2, C3.2, C4.2, C5.1, C6.2, C7.2, C8.2, C9.2, C10.1, C11.2, C12.2, C13.2, C14.2, C15.2, C16.2, C17.2, C18.2, C19.2, C20.2, C66.2, C75.2, JTAG.3, JTAG.5, JTAG.7, JTAG.9, R3.2, TG7.TP, U1.10 (VSS1), U1.20 (VSSA), U1.27 (VSS2), U1.74 (VSS3), U1.99 (RFU), U9.6 (GND), U9.GND1 (SHIELD), U9.GND3 (SHIELD), USB3.5, USB3.GND1, USB3.GND2, USB3.GND3, USB3.GND4; also elsewhere on the board
I2C2_SCL: U1.47 (PB10); also elsewhere on the board
I2C2_SDA: U1.48 (PB11); also elsewhere on the board
IMU_ACC_CS: U1.51 (PB12); also elsewhere on the board
IMU_ACC_DRDY: U1.98 (PE1); also elsewhere on the board
IMU_GYRO_DRDY: U1.1 (PE2); also elsewhere on the board
IMU_GYRO_SS: U1.2 (PE3); also elsewhere on the board
IMU_MAG_DRDY: U1.97 (PE0); also elsewhere on the board
IMU_SPI_MISO: U1.53 (PB14); also elsewhere on the board
IMU_SPI_MOSI: U1.54 (PB15); also elsewhere on the board
IMU_SPI_SCK: U1.52 (PB13); also elsewhere on the board
JTAG_RST: C8.1, JTAG.10, R2.2, TP2.TP, U1.14 (NRST)
JTAG_TCK/SWCLK: JTAG.4, TP3.TP, U1.76 (PA14)
JTAG_TDI: TP6.TP, U1.77 (PA15)
JTAG_TDO/TRACESWO: TP7.TP, U1.89 (PB3)
JTAG_TMS/SWDIO: JTAG.2, TP1.TP, U1.72 (PA13)
MCU_D_N: U1.70 (PA11), USB3.2
MCU_D_P: U1.71 (PA12), USB3.3
MCU_VBUS: D3.A, USB3.1
unnamed: C19.1, U1.49 (VCAP_1)
unnamed: C20.1, U1.73 (VCAP_2)
unnamed: C10.2, Q1.2, U1.12 (PH0-OSC_IN)
unnamed: R3.1, U1.94 (BOOT0)
SD_CLK: TP49.TP, U1.80 (PC12), U9.5 (SCK)
SD_CMD: TP48.TP, U1.83 (PD2), U9.3 (DI)
SD_D0: TP50.TP, U1.65 (PC8), U9.7 (DO)
SD_D1: TP61.TP, U1.66 (PC9), U9.8 (RSV)
SD_D2: TP62.TP, U1.78 (PC10), U9.1 (NC)
SD_D3: TP57.TP, U1.79 (PC11), U9.2 (CS)
SD_SW: TP63.TP, U1.67 (PA8), U9.CD1 (SHIELD)
UART1_RX: R5.2, U1.69 (PA10); also elsewhere on the board
UART1_TX: U1.68 (PA9); also elsewhere on the board
UART2_RX: R14.2, U1.87 (PD6); also elsewhere on the board
UART2_TX: U1.86 (PD5); also elsewhere on the board
UART3_RX: R4.2, U1.56 (PD9); also elsewhere on the board
UART3_TX: U1.55 (PD8); also elsewhere on the board
UART6_RX: R15.2, U1.64 (PC7); also elsewhere on the board
UART6_TX: U1.63 (PC6); also elsewhere on the board
VDDA: C3.1, C6.1, L1.P$2 (2), R1.1, U1.22 (VDDA)
VREF+: R1.2, U1.21 (VREF+)
V_IN: D3.C; also elsewhere on the board
XLT: C5.2, Q1.1, U1.13 (PH1-OSC_OUT)

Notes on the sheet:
JTAG
MCU
MCU PWR
PULL-UPS
more UARTS
SD Card MCU
Switch already connected to GND via pin 9 (see datasheet for 10100581)
extra cap just in case

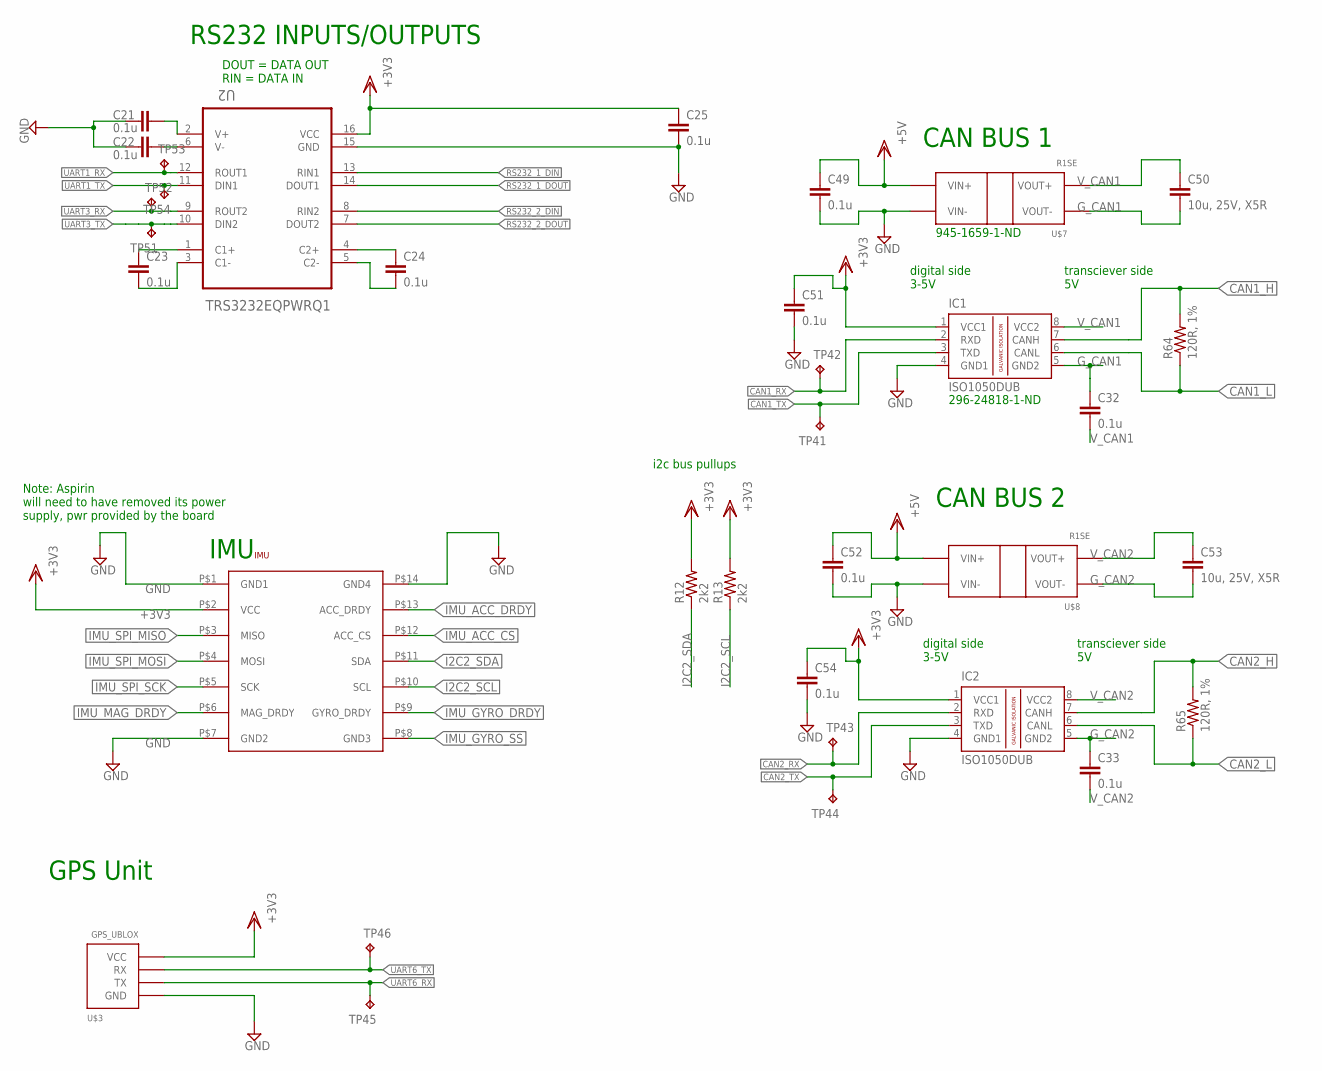
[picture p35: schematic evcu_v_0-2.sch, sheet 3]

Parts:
C21, C22, C23, C24, C25, C32, C33, C49, C51, C52, C54: 0.1u; C0603@1
C50, C53: 10u, 25V, X5R; C0603@1
IC1, IC2: ISO1050DUB; DUB-R-PDSO-G8
IMU: ASPIRIN; ASPIRIN_1; PARTNO ASP6000
R12, R13: 2k2; R0603
R64, R65: 120R, 1%; R0603
TP41, TP42, TP43, TP44, TP45, TP46, TP51, TP52, TP53, TP54: TPB1,27; B1,27
U2: TRS3232EQPWRQ1; SOP65P640X120-16N; DIGIKEY 296-24863-1-ND
U$3: GPS_UBLOX
U$7, U$8: R1SE

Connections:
5V: C49.1, C52.1, U$7.P2 (VIN+), U$8.P2 (VIN+); also elsewhere on the board
+3V3: C25.1, C51.1, C54.1, IC1.1 (VCC1), IC2.1 (VCC1), IMU.P$2 (VCC), R12.2, R13.2, U2.16 (VCC), U$3.VCC; also elsewhere on the board
CAN1_H: IC1.7 (CANH), R64.2; also elsewhere on the board
CAN1_L: IC1.6 (CANL), R64.1; also elsewhere on the board
CAN1_RX: IC1.2 (RXD), TP42.TP; also elsewhere on the board
CAN1_TX: IC1.3 (TXD), TP41.TP; also elsewhere on the board
CAN2_H: IC2.7 (CANH), R65.2; also elsewhere on the board
CAN2_L: IC2.6 (CANL), R65.1; also elsewhere on the board
CAN2_RX: IC2.2 (RXD), TP43.TP; also elsewhere on the board
CAN2_TX: IC2.3 (TXD), TP44.TP; also elsewhere on the board
GND: C21.1, C22.1, C25.2, C49.2, C51.2, C52.2, C54.2, IC1.4 (GND1), IC2.4 (GND1), IMU.P$1 (GND1), IMU.P$7 (GND2), IMU.P$14 (GND4), U2.15 (GND), U$3.GND, U$7.P1 (VIN-), U$8.P1 (VIN-); also elsewhere on the board
G_CAN1: C32.1, C50.2, IC1.5 (GND2), U$7.P4 (VOUT-)
G_CAN2: C33.1, C53.2, IC2.5 (GND2), U$8.P4 (VOUT-)
I2C2_SCL: IMU.P$10 (SCL), R13.1; also elsewhere on the board
I2C2_SDA: IMU.P$11 (SDA), R12.1; also elsewhere on the board
IMU_ACC_CS: IMU.P$12 (ACC_CS); also elsewhere on the board
IMU_ACC_DRDY: IMU.P$13 (ACC_DRDY); also elsewhere on the board
IMU_GYRO_DRDY: IMU.P$9 (GYRO_DRDY); also elsewhere on the board
IMU_GYRO_SS: IMU.P$8 (GND3); also elsewhere on the board
IMU_MAG_DRDY: IMU.P$6 (MAG_DRDY); also elsewhere on the board
IMU_SPI_MISO: IMU.P$3 (MISO); also elsewhere on the board
IMU_SPI_MOSI: IMU.P$4 (MOSI); also elsewhere on the board
IMU_SPI_SCK: IMU.P$5 (SCK); also elsewhere on the board
unnamed: C24.1, U2.4 (C2+)
unnamed: C24.2, U2.5 (C2-)
unnamed: C23.1, U2.1 (C1+)
unnamed: C23.2, U2.3 (C1-)
unnamed: C21.2, U2.2 (V+)
unnamed: C22.2, U2.6 (V-)
RS232_1_DIN: U2.13 (RIN1); also elsewhere on the board
RS232_1_DOUT: U2.14 (DOUT1); also elsewhere on the board
RS232_2_DIN: U2.8 (RIN2); also elsewhere on the board
RS232_2_DOUT: U2.7 (DOUT2); also elsewhere on the board
UART1_RX: TP53.TP, U2.12 (ROUT1); also elsewhere on the board
UART1_TX: TP54.TP, U2.11 (DIN1); also elsewhere on the board
UART3_RX: TP52.TP, U2.9 (ROUT2); also elsewhere on the board
UART3_TX: TP51.TP, U2.10 (DIN2); also elsewhere on the board
UART6_RX: TP45.TP, U$3.TX; also elsewhere on the board
UART6_TX: TP46.TP, U$3.RX; also elsewhere on the board
V_CAN1: C32.2, C50.1, IC1.8 (VCC2), U$7.P5 (VOUT+)
V_CAN2: C33.2, C53.1, IC2.8 (VCC2), U$8.P5 (VOUT+)

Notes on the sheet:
RS232 INPUTS/OUTPUTS
DOUT = DATA OUT RIN = DATA IN
IMU
GPS Unit
Note: Aspirin will need to have removed its power supply, pwr provided by the board
CAN BUS 1
digital side 3-5V
transciever side 5V
CAN BUS 2
945-1659-1-ND
296-24818-1-ND
i2c bus pullups

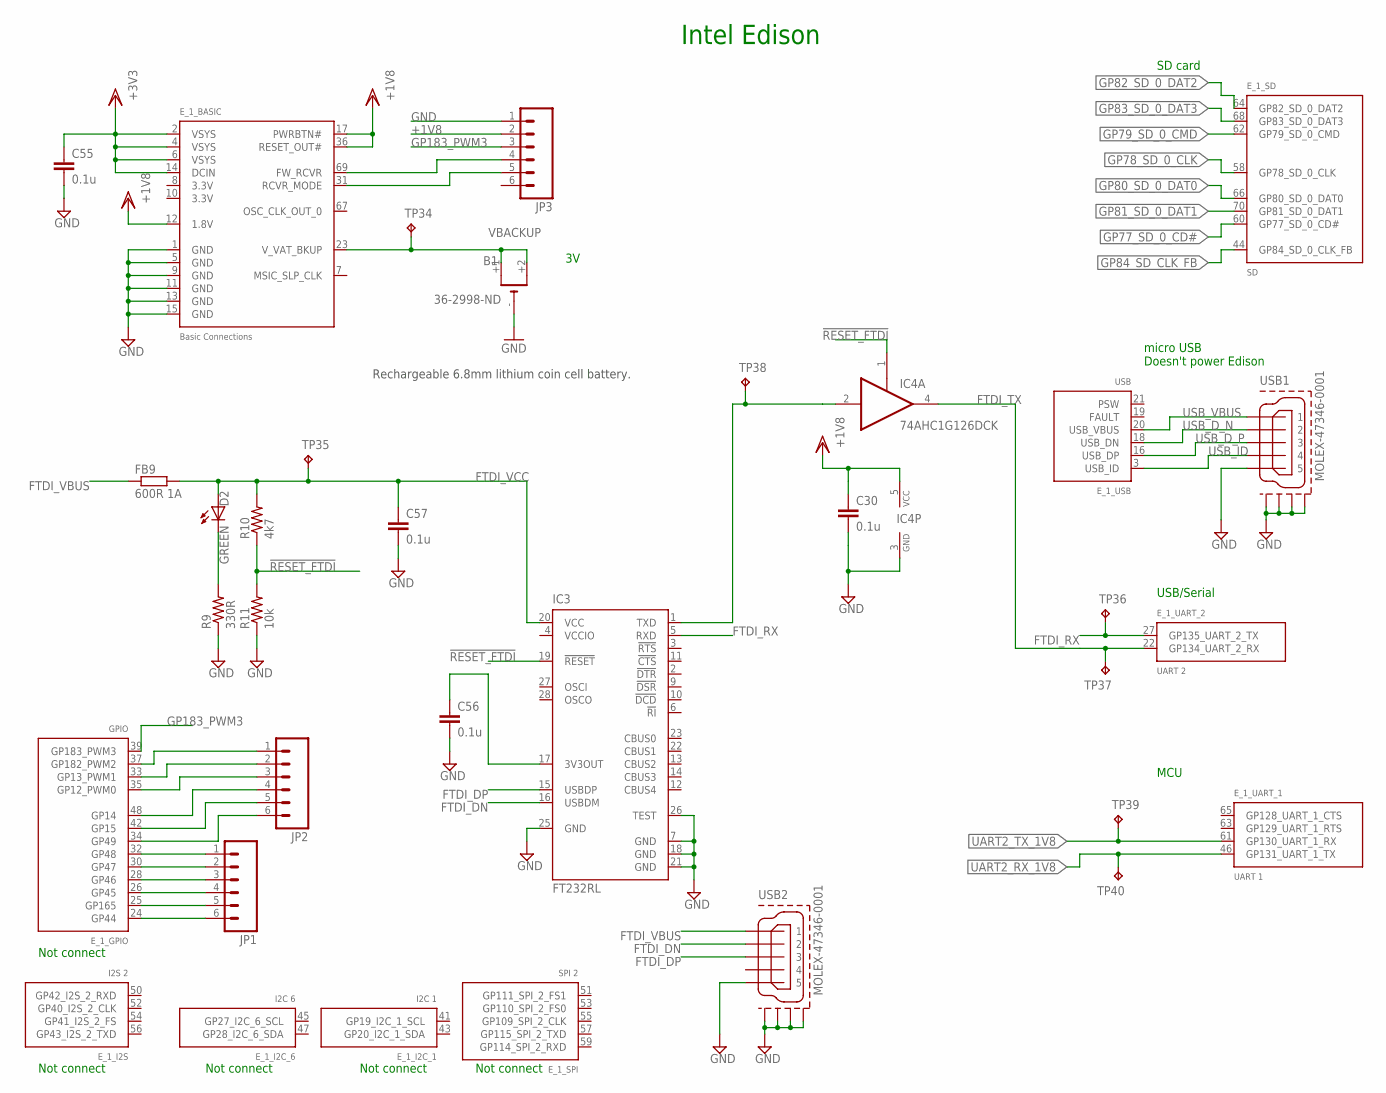
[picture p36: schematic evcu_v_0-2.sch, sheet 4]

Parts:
B1: 36-2998-ND; BATTERY_6.8MM-2998
C30, C55, C56, C57: 0.1u; C0603@1
D2: GREEN; D0603
E_1: EDISON_CONNECTOR_SEGMENTED; EDISON_DAUGHTER
FB9: 600R 1A; C0603
IC3: FT232RL; SSOP28
IC4: 74AHC1G126DCK; SC70-5
JP1, JP2, JP3: M06SIP; 1X06
R9: 330R; R0603
R10: 4k7; R0603
R11: 10k; R0603
TP34, TP35, TP36, TP37, TP38, TP39, TP40: TPB1,27; B1,27
USB1, USB2: MOLEX-47346-0001; MOLEX-47364-0001

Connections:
!RESET_FTDI: IC3.19 (!RESET), IC4.1 (OE), R10.1, R11.2
+1V8: C30.1, E_1.12 (1.8V), E_1.17 (PWRBTN#), E_1.36 (RESET_OUT#), IC4.5 (VCC), JP3.2; also elsewhere on the board
+3V3: C55.1, E_1.2 (VSYS), E_1.4 (VSYS), E_1.6 (VSYS), E_1.14 (DCIN); also elsewhere on the board
FTDI_DN: IC3.16 (USBDM), USB2.2
FTDI_DP: IC3.15 (USBDP), USB2.3
FTDI_RX: E_1.27 (GP135_UART_2_TX), IC3.5 (RXD), TP36.TP
FTDI_TX: E_1.22 (GP134_UART_2_RX), IC4.4 (O), TP37.TP
FTDI_VBUS: FB9.1, USB2.1
FTDI_VCC: C57.1, D2.A, FB9.2, IC3.20 (VCC), R10.2, TP35.TP
FW_RCVR: E_1.69 (FW_RCVR), JP3.4
GND: B1.-, C30.2, C55.2, C56.2, C57.2, E_1.1 (GND), E_1.5 (GND), E_1.9 (GND), E_1.11 (GND), E_1.13 (GND), E_1.15 (GND), IC3.7 (GND), IC3.18 (GND), IC3.21 (GND), IC3.25 (GND), IC3.26 (TEST), IC4.3 (GND), JP3.1, R9.1, R11.1, USB1.5, USB1.GND1, USB1.GND2, USB1.GND3, USB1.GND4, USB2.5, USB2.GND1, USB2.GND2, USB2.GND3, USB2.GND4; also elsewhere on the board
GP12: E_1.35 (GP12_PWM0), JP2.3
GP13: E_1.33 (GP13_PWM1), JP2.2
GP14: E_1.48 (GP14), JP2.4
GP15: E_1.42 (GP15), JP2.5
GP44: E_1.24 (GP44), JP1.6
GP45: E_1.26 (GP45), JP1.4
GP46: E_1.28 (GP46), JP1.3
GP47: E_1.30 (GP47), JP1.2
GP48: E_1.32 (GP48), JP1.1
GP49: E_1.34 (GP49), JP2.6
GP77_SD_0_CD#: E_1.60 (GP77_SD_0_CD#); also elsewhere on the board
GP78_SD_0_CLK: E_1.58 (GP78_SD_0_CLK); also elsewhere on the board
GP79_SD_0_CMD: E_1.62 (GP79_SD_0_CMD); also elsewhere on the board
GP80_SD_0_DAT0: E_1.66 (GP80_SD_0_DAT0); also elsewhere on the board
GP81_SD_0_DAT1: E_1.70 (GP81_SD_0_DAT1); also elsewhere on the board
GP82_SD_0_DAT2: E_1.64 (GP82_SD_0_DAT2); also elsewhere on the board
GP83_SD_0_DAT3: E_1.68 (GP83_SD_0_DAT3); also elsewhere on the board
GP84_SD_CLK_FB: E_1.44 (GP84_SD_0_CLK_FB); also elsewhere on the board
GP165: E_1.25 (GP165), JP1.5
GP182: E_1.37 (GP182_PWM2), JP2.1
GP183_PWM3: E_1.39 (GP183_PWM3), JP3.3
LED1_PWR: D2.C, R9.2
unnamed: C56.1, IC3.17 (3V3OUT)
unnamed: IC3.1 (TXD), IC4.2 (I), TP38.TP
RCVR_MODE: E_1.31 (RCVR_MODE), JP3.5
UART2_RX_1V8: E_1.46 (GP131_UART_1_TX), TP40.TP; also elsewhere on the board
UART2_TX_1V8: E_1.61 (GP130_UART_1_RX), TP39.TP; also elsewhere on the board
USB_D_N: E_1.18 (USB_DN), USB1.2
USB_D_P: E_1.16 (USB_DP), USB1.3
USB_ID: E_1.3 (USB_ID), USB1.4
USB_VBUS: E_1.20 (USB_VBUS), USB1.1
VBACKUP: B1.+1, B1.+2, E_1.23 (V_VAT_BKUP), TP34.TP
VCCIO: IC3.4 (VCCIO)

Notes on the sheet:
Intel Edison
micro USB Doesn't power Edison
Not connect
MCU
USB/Serial
SD card
Rechargeable 6.8mm lithium coin cell battery.

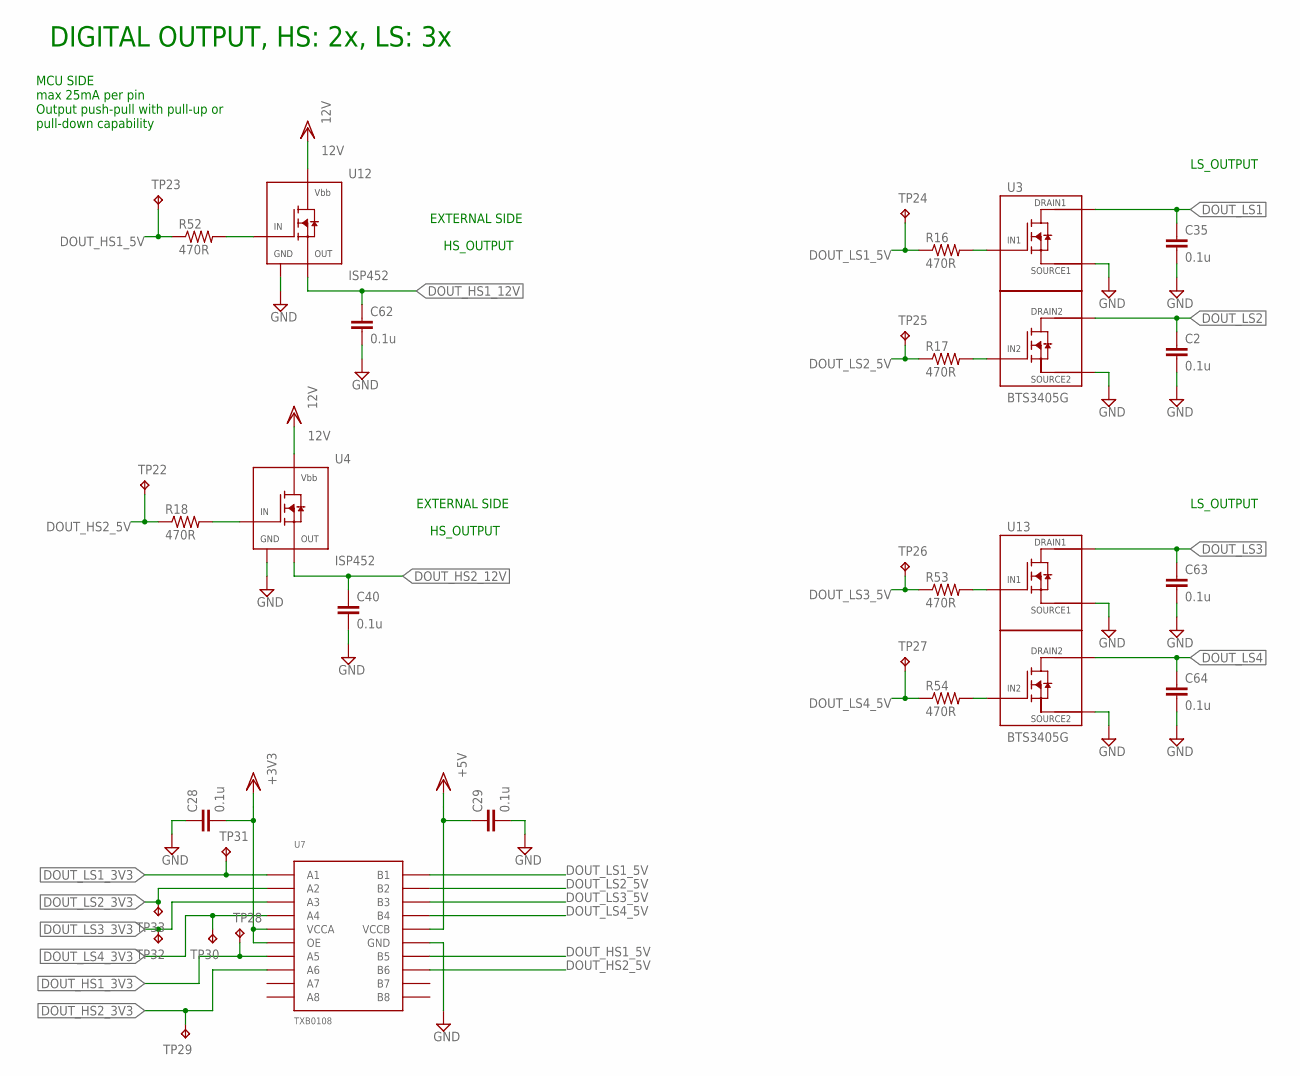
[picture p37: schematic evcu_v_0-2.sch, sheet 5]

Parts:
C2, C28, C29, C35, C40, C62, C63, C64: 0.1u; C0603@1
R16, R17, R18, R52, R53, R54: 470R; R0603
TP22, TP23, TP24, TP25, TP26, TP27, TP28, TP29, TP30, TP31, TP32, TP33: TPB1,27; B1,27
U3, U13: BTS3405G; SOIC8
U4, U12: ISP452; SOT223-W
U7: TXB0108; TSSOP20

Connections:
5V: C29.1, U7.19 (VCCB); also elsewhere on the board
12V: U4.4 (VBB), U12.4 (VBB); also elsewhere on the board
+3V3: C28.2, U7.2 (VCCA), U7.10 (OE); also elsewhere on the board
DOUT_HS1_3V3: TP28.TP, U7.6 (A5); also elsewhere on the board
DOUT_HS1_5V: R52.1, TP23.TP, U7.15 (B5)
DOUT_HS1_12V: C62.1, U12.1 (OUT); also elsewhere on the board
DOUT_HS2_3V3: TP29.TP, U7.7 (A6); also elsewhere on the board
DOUT_HS2_5V: R18.1, TP22.TP, U7.14 (B6)
DOUT_HS2_12V: C40.1, U4.1 (OUT); also elsewhere on the board
DOUT_LS1: C35.1, U3.7 (DRAIN1), U3.8 (DRAIN1); also elsewhere on the board
DOUT_LS1_3V3: TP31.TP, U7.1 (A1); also elsewhere on the board
DOUT_LS1_5V: R16.1, TP24.TP, U7.20 (B1)
DOUT_LS2: C2.1, U3.5 (DRAIN2), U3.6 (DRAIN2); also elsewhere on the board
DOUT_LS2_3V3: TP33.TP, U7.3 (A2); also elsewhere on the board
DOUT_LS2_5V: R17.1, TP25.TP, U7.18 (B2)
DOUT_LS3: C63.1, U13.7 (DRAIN1), U13.8 (DRAIN1); also elsewhere on the board
DOUT_LS3_3V3: TP32.TP, U7.4 (A3); also elsewhere on the board
DOUT_LS3_5V: R53.1, TP26.TP, U7.17 (B3)
DOUT_LS4: C64.1, U13.5 (DRAIN2), U13.6 (DRAIN2); also elsewhere on the board
DOUT_LS4_3V3: TP30.TP, U7.5 (A4); also elsewhere on the board
DOUT_LS4_5V: R54.1, TP27.TP, U7.16 (B4)
GND: C2.2, C28.1, C29.2, C35.2, C40.2, C62.2, C63.2, C64.2, U3.1 (SOURCE1), U3.3 (SOURCE2), U4.2 (GND), U7.11 (GND), U12.2 (GND), U13.1 (SOURCE1), U13.3 (SOURCE2); also elsewhere on the board
unnamed: R16.2, U3.2 (IN1)
unnamed: R17.2, U3.4 (IN2)
unnamed: R18.2, U4.3 (IN)
unnamed: R52.2, U12.3 (IN)
unnamed: R53.2, U13.2 (IN1)
unnamed: R54.2, U13.4 (IN2)

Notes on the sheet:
DIGITAL OUTPUT, HS: 2x, LS: 3x
MCU SIDE max 25mA per pin Output push-pull with pull-up or pull-down capability
EXTERNAL SIDE
HS_OUTPUT
LS_OUTPUT

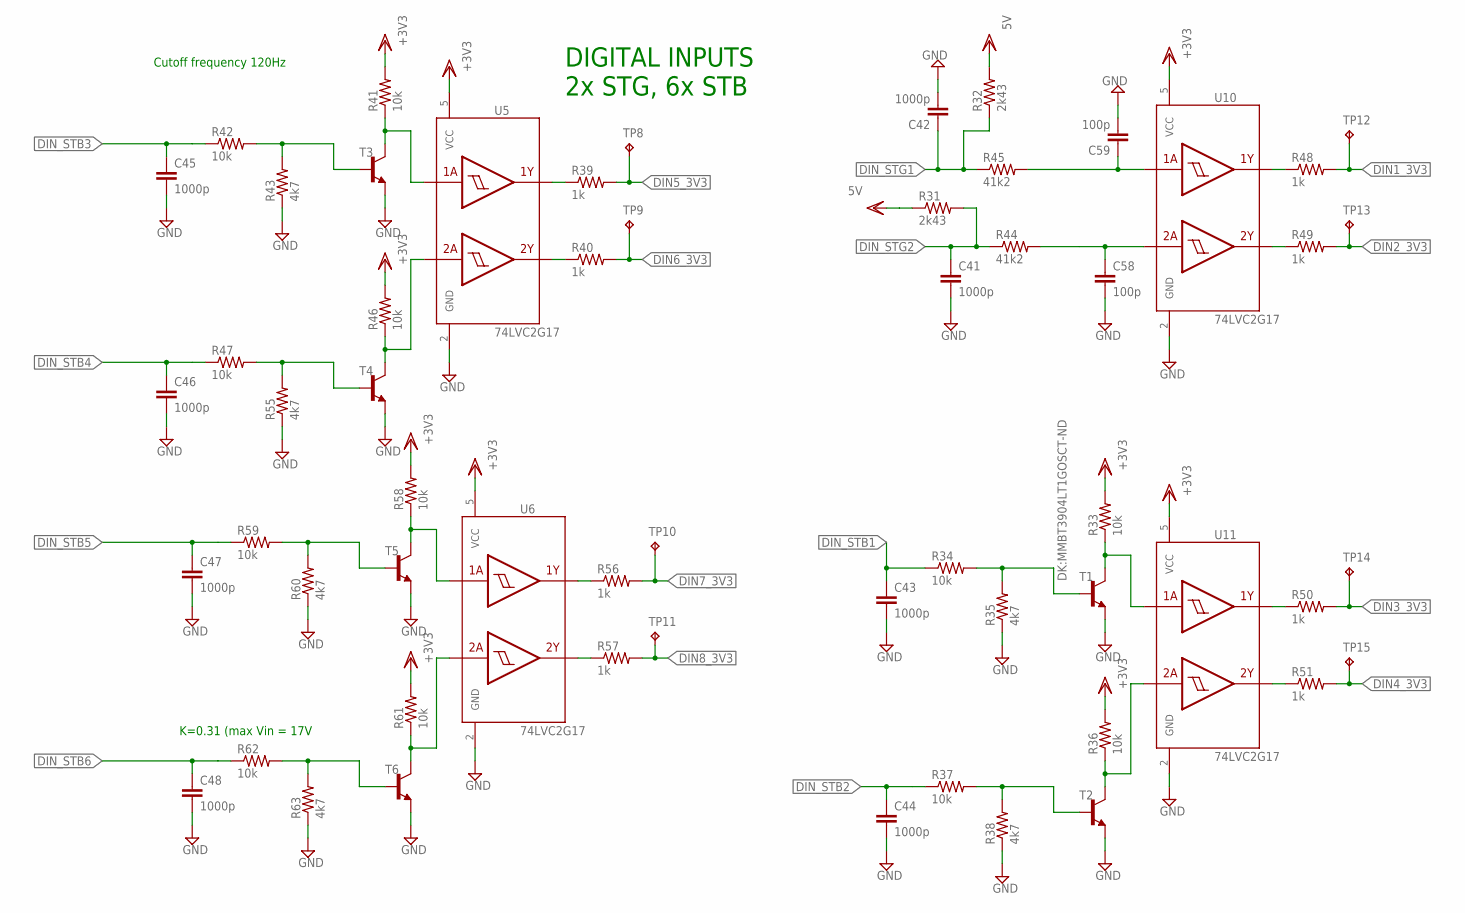
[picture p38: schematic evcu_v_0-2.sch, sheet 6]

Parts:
C41, C42, C43, C44, C45, C46, C47, C48: 1000p; C0603@1
C58, C59: 100p; C0603@1
R31, R32: 2k43; R0603
R33, R34, R36, R37, R41, R42, R46, R47, R58, R59, R61, R62: 10k; R0603
R35, R38, R43, R55, R60, R63: 4k7; R0603
R39, R40, R48, R49, R50, R51, R56, R57: 1k; R0603
R44, R45: 41k2; R0603
T1, T2, T3, T4, T5, T6: DK:MMBT3904LT1GOSCT-ND; SOT23-BEC
TP8, TP9, TP10, TP11, TP12, TP13, TP14, TP15: TPB1,27; B1,27
U5, U6, U10, U11: 74LVC2G17; SOT363_INFINEON

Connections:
5V: R31.1, R32.2; also elsewhere on the board
+3V3: R33.2, R36.2, R41.2, R46.2, R58.2, R61.2, U5.5 (VCC), U6.5 (VCC), U10.5 (VCC), U11.5 (VCC); also elsewhere on the board
DIN1_3V3: R48.2, TP12.TP; also elsewhere on the board
DIN2_3V3: R49.2, TP13.TP; also elsewhere on the board
DIN3_3V3: R50.2, TP14.TP; also elsewhere on the board
DIN4_3V3: R51.2, TP15.TP; also elsewhere on the board
DIN5_3V3: R39.2, TP8.TP; also elsewhere on the board
DIN6_3V3: R40.2, TP9.TP; also elsewhere on the board
DIN7_3V3: R56.2, TP10.TP; also elsewhere on the board
DIN8_3V3: R57.2, TP11.TP; also elsewhere on the board
DIN_STB1: C43.1, R34.1; also elsewhere on the board
DIN_STB2: C44.1, R37.1; also elsewhere on the board
DIN_STB3: C45.1, R42.1; also elsewhere on the board
DIN_STB4: C46.1, R47.1; also elsewhere on the board
DIN_STB5: C47.1, R59.1; also elsewhere on the board
DIN_STB6: C48.1, R62.1; also elsewhere on the board
DIN_STG1: C42.1, R32.1, R45.1; also elsewhere on the board
DIN_STG2: C41.1, R31.2, R44.1; also elsewhere on the board
GND: C41.2, C42.2, C43.2, C44.2, C45.2, C46.2, C47.2, C48.2, C58.2, C59.2, R35.1, R38.1, R43.1, R55.1, R60.1, R63.1, T1.E, T2.E, T3.E, T4.E, T5.E, T6.E, U5.2 (GND), U6.2 (GND), U10.2 (GND), U11.2 (GND); also elsewhere on the board
unnamed: R33.1, T1.C, U11.1 (1A)
unnamed: R36.1, T2.C, U11.3 (2A)
unnamed: R39.1, U5.6 (1Y)
unnamed: R40.1, U5.4 (2Y)
unnamed: R41.1, T3.C, U5.1 (1A)
unnamed: R46.1, T4.C, U5.3 (2A)
unnamed: R56.1, U6.6 (1Y)
unnamed: R57.1, U6.4 (2Y)
unnamed: R58.1, T5.C, U6.1 (1A)
unnamed: R61.1, T6.C, U6.3 (2A)
unnamed: R49.1, U10.4 (2Y)
unnamed: R48.1, U10.6 (1Y)
unnamed: R50.1, U11.6 (1Y)
unnamed: R51.1, U11.4 (2Y)
TVS1: C58.1, R44.2, U10.3 (2A)
TVS2: C59.1, R45.2, U10.1 (1A)
TVS3: R34.2, R35.2, T1.B
TVS4: R37.2, R38.2, T2.B
TVS5: R42.2, R43.2, T3.B
TVS6: R47.2, R55.2, T4.B
TVS7: R59.2, R60.2, T5.B
TVS8: R62.2, R63.2, T6.B

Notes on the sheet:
DIGITAL INPUTS 2x STG, 6x STB
Cutoff frequency 120Hz
K=0.31 (max Vin = 17V

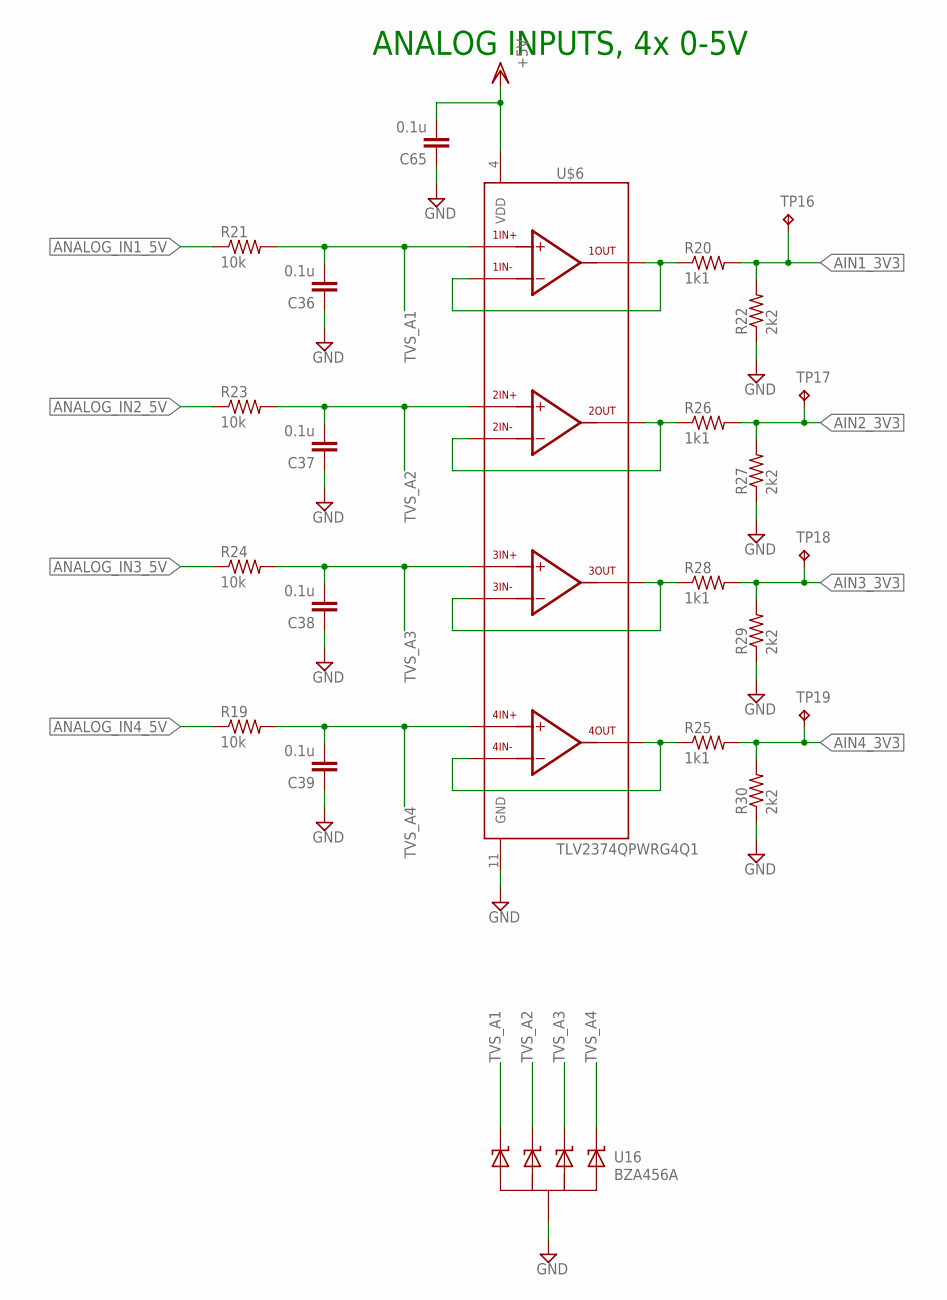
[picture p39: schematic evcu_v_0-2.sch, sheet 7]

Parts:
C36, C37, C38, C39, C65: 0.1u; C0603@1
R19, R21, R23, R24: 10k; R0603
R20, R25, R26, R28: 1k1; R0603
R22, R27, R29, R30: 2k2; R0603
TP16, TP17, TP18, TP19: TPB1,27; B1,27
U16: BZA456A; SOT457R_PHILIPS
U$6: TLV2374QPWRG4Q1; TSSOP14

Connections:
5V: C65.2, U$6.4 (VDD); also elsewhere on the board
AIN1_3V3: R20.2, R22.2, TP16.TP; also elsewhere on the board
AIN2_3V3: R26.2, R27.2, TP17.TP; also elsewhere on the board
AIN3_3V3: R28.2, R29.2, TP18.TP; also elsewhere on the board
AIN4_3V3: R25.2, R30.2, TP19.TP; also elsewhere on the board
ANALOG_IN1_5V: R21.1; also elsewhere on the board
ANALOG_IN2_5V: R23.1; also elsewhere on the board
ANALOG_IN3_5V: R24.1; also elsewhere on the board
ANALOG_IN4_5V: R19.1; also elsewhere on the board
GND: C36.1, C37.1, C38.1, C39.1, C65.1, R22.1, R27.1, R29.1, R30.1, U16.2 (COM), U16.5 (COM), U$6.11 (GND); also elsewhere on the board
unnamed: R25.1, U$6.13, U$6.14
unnamed: R20.1, U$6.1, U$6.2
unnamed: R26.1, U$6.6, U$6.7
unnamed: R28.1, U$6.8, U$6.9
TVS_A1: C36.2, R21.2, U16.1 (C1), U$6.3
TVS_A2: C37.2, R23.2, U16.3 (C2), U$6.5
TVS_A3: C38.2, R24.2, U16.4 (C3), U$6.10
TVS_A4: C39.2, R19.2, U16.6 (C4), U$6.12

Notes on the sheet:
ANALOG INPUTS, 4x 0-5V


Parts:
C61, C67, C74: 0.1u; C0603@1
R6, R72: 470R; R0603
R7, R71: 1k1; R0603
R8, R70: 2k2; R0603
TP20, TP21: TPB1,27; B1,27
U8: BZA456A; SOT457R_PHILIPS
U$2: TLV2374QPWRG4Q1; TSSOP14

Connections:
5V: C74.2, U$2.4 (VDD); also elsewhere on the board
AN_OUT1_5V: R72.2; also elsewhere on the board
AN_OUT2_5V: R6.2; also elsewhere on the board
DAC1_3V3: TP21.TP, U$2.12; also elsewhere on the board
DAC2_3V3: TP20.TP, U$2.10; also elsewhere on the board
GND: C61.1, C67.1, C74.1, R8.1, R70.1, U8.2 (COM), U8.5 (COM), U$2.11 (GND); also elsewhere on the board
unnamed: R7.1, R8.2, U$2.9
unnamed: R70.2, R71.1, U$2.13
TVS_A5: C67.2, R71.2, R72.1, U8.6 (C4), U$2.14
TVS_A6: C61.2, R6.1, R7.2, U8.4 (C3), U$2.8

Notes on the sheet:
ANALOG OUTPUT, 2x 0-5V
Vout = (1+R0/R1)*V_in R0=1k1 R1=2k2

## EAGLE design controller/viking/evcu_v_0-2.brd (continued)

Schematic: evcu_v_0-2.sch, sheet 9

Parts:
U$5: DEUTSCH_48_PIN

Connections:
5V: U$5.A$2, U$5.A$5, U$5.A$8, U$5.A$11; also elsewhere on the board
ANALOG_IN1_5V: U$5.A$3; also elsewhere on the board
ANALOG_IN2_5V: U$5.A$6; also elsewhere on the board
ANALOG_IN3_5V: U$5.A$9; also elsewhere on the board
ANALOG_IN4_5V: U$5.A$12; also elsewhere on the board
AN_OUT1_5V: U$5.C$2; also elsewhere on the board
AN_OUT2_5V: U$5.C$4; also elsewhere on the board
CAN1_H: U$5.C$7; also elsewhere on the board
CAN1_L: U$5.C$8; also elsewhere on the board
CAN2_H: U$5.C$11; also elsewhere on the board
CAN2_L: U$5.C$12; also elsewhere on the board
DIN_STB1: U$5.B$7; also elsewhere on the board
DIN_STB2: U$5.B$8; also elsewhere on the board
DIN_STB3: U$5.B$9; also elsewhere on the board
DIN_STB4: U$5.B$10; also elsewhere on the board
DIN_STB5: U$5.B$11; also elsewhere on the board
DIN_STB6: U$5.B$12; also elsewhere on the board
DIN_STG1: U$5.B$2; also elsewhere on the board
DIN_STG2: U$5.B$4; also elsewhere on the board
DOUT_HS1_12V: U$5.D$11; also elsewhere on the board
DOUT_HS2_12V: U$5.D$12; also elsewhere on the board
DOUT_LS1: U$5.D$7; also elsewhere on the board
DOUT_LS2: U$5.D$8; also elsewhere on the board
DOUT_LS3: U$5.D$9; also elsewhere on the board
DOUT_LS4: U$5.D$10; also elsewhere on the board
GND: U$5.A$1, U$5.A$4, U$5.A$7, U$5.A$10, U$5.B$1, U$5.B$3, U$5.B$5, U$5.C$1, U$5.C$3, U$5.C$5, U$5.C$9, U$5.D$1, U$5.D$4; also elsewhere on the board
RS232_1_DIN: U$5.D$2; also elsewhere on the board
RS232_1_DOUT: U$5.D$3; also elsewhere on the board
RS232_2_DIN: U$5.D$5; also elsewhere on the board
RS232_2_DOUT: U$5.D$6; also elsewhere on the board
VIN(+12V): U$5.B$6, U$5.C$6, U$5.C$10; also elsewhere on the board

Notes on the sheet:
DEUTSCH 48pin header DEUTSCH EEC-5X650B DEUTSCH DT13-48PABCD-R015


Board: 4 copper layers, 156.2 x 127.0 mm, 267 parts (0 on the bottom side), 204 nets.

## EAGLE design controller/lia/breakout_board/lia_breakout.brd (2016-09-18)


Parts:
J1, J2, J3, J4, J5, J6, J7, J8: CONN_3-1; SIP1X3_100; PARTNO conn-th-0.1in-3-2-ra

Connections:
GND: J1.1, J2.1, J3.1, J4.1, J5.1, J6.1, J7.1, J8.1; also elsewhere on the board
S1: J1.3
S2: J2.3
S3: J3.3
S4: J4.3
S5: J5.3
S6: J6.3
S7: J7.3
S8: J8.3

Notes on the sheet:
Servos Connectors


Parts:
JP14, JP15, JP16, JP17: PINHD-1X4; 1X04; PARTNO conn-th-0.1in-4-1
JP20: PINHD-1X6; 1X06; PARTNO conn-th-0.1in-6-1
JP21, JP22: PINHD-1X7; 1X07; PARTNO conn-th-0.1in-7-1

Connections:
EXTSPI_DRDY: JP22.7
EXTSPI_MISO: JP22.4
EXTSPI_MOSI: JP22.3
EXTSPI_SCK: JP22.5
EXTSPI_SS: JP22.6
GND: JP14.1, JP15.1, JP16.1, JP17.1, JP20.1, JP20.4, JP21.1, JP22.1; also elsewhere on the board
I2C2_SCL: JP14.3
I2C2_SDA: JP14.4
JTAG_TRST: JP15.4
PC12_UART5_TX: JP15.3; also elsewhere on the board
UART1_RX_I2C1_SDA: JP21.7; also elsewhere on the board
UART1_TX_I2C1_SCL: JP21.6; also elsewhere on the board
UART2_RX: JP16.4; also elsewhere on the board
UART2_TX: JP16.3; also elsewhere on the board
UART3_RX: JP17.4; also elsewhere on the board
UART3_TX: JP17.3; also elsewhere on the board
UART5_RX: JP20.6; also elsewhere on the board

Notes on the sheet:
SPI
I2C2
GPIO1
UART3
UART2
RC RX\
CAN/I2C1


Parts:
C1, C2, C3, C6, C7, C9, C10, C12: 0.1uF; 0603-CAP
C4, C5, C8, C11: 10uF; C0603
LED1, LED3, LED5, LED7: Red; LED-0603
LED2, LED4, LED6, LED8: Green; LED-0603
R1, R2, R3, R4, R5, R6, R7, R8: 1K; 0603-RES
U1, U2, U3, U5: FT232RLSSOP; SSOP28DB
X1, X2, X3, X4: USB-SMD-NS; USB-MINIB-NOSTOP

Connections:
3.3V1: C6.1, U1.17 (3V3OUT)
3.3V2: C1.1, U2.17 (3V3OUT)
3.3V3: C9.1, U3.17 (3V3OUT)
3.3V5: C12.1, U5.17 (3V3OUT)
5V1: C3.1, C4.1, R3.2, R4.2, U1.20 (VCC), X1.VBUS
5V2: C2.1, C5.1, R1.2, R2.2, U2.20 (VCC), X2.VBUS
5V3: C7.1, C8.1, R5.2, R6.2, U3.20 (VCC), X3.VBUS
5V5: C10.1, C11.1, R7.2, R8.2, U5.20 (VCC), X4.VBUS
GND: C1.2, C2.2, C3.2, C4.2, C5.2, C6.2, C7.2, C8.2, C9.2, C10.2, C11.2, C12.2, U1.7 (GND7), U1.18 (GND18), U1.21 (GND21), U1.25 (AGND), U1.26 (TEST), U2.7 (GND7), U2.18 (GND18), U2.21 (GND21), U2.25 (AGND), U2.26 (TEST), U3.7 (GND7), U3.18 (GND18), U3.21 (GND21), U3.25 (AGND), U3.26 (TEST), U5.7 (GND7), U5.18 (GND18), U5.21 (GND21), U5.25 (AGND), U5.26 (TEST), X1.GND, X2.GND, X3.GND, X4.GND; also elsewhere on the board
unnamed: LED1.A, R1.1
unnamed: LED2.A, R2.1
unnamed: LED3.A, R3.1
unnamed: LED4.A, R4.1
unnamed: LED5.A, R5.1
unnamed: LED6.A, R6.1
unnamed: LED7.A, R7.1
unnamed: LED8.A, R8.1
PC12_UART5_TX: U5.5 (RXD); also elsewhere on the board
RXLED1: LED4.C, U1.22 (RXLED)
RXLED2: LED2.C, U2.22 (RXLED)
RXLED3: LED6.C, U3.22 (RXLED)
RXLED5: LED8.C, U5.22 (RXLED)
TXLED1: LED3.C, U1.23 (TXLED)
TXLED2: LED1.C, U2.23 (TXLED)
TXLED3: LED5.C, U3.23 (TXLED)
TXLED5: LED7.C, U5.23 (TXLED)
UART1_RX_I2C1_SDA: U1.1 (TXD); also elsewhere on the board
UART1_TX_I2C1_SCL: U1.5 (RXD); also elsewhere on the board
UART2_RX: U2.1 (TXD); also elsewhere on the board
UART2_TX: U2.5 (RXD); also elsewhere on the board
UART3_RX: U3.1 (TXD); also elsewhere on the board
UART3_TX: U3.5 (RXD); also elsewhere on the board
UART5_RX: U5.1 (TXD); also elsewhere on the board
USB_D+: U2.15 (USBDP), X2.D+
USB_D+1: U1.15 (USBDP), X1.D+
USB_D+2: U3.15 (USBDP), X3.D+
USB_D+3: U5.15 (USBDP), X4.D+
USB_D-: U2.16 (USBDM), X2.D-
USB_D-1: U1.16 (USBDM), X1.D-
USB_D-2: U3.16 (USBDM), X3.D-
USB_D-3: U5.16 (USBDM), X4.D-

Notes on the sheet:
UART1 - XGEAR
UART3 - Telemetry
UART2 - VectorNav
UART5 - SBUS


Board: 2 copper layers, 72.4 x 78.7 mm, 55 parts (0 on the bottom side), 41 nets.

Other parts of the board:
U$13, U$14, U$15, U$16: 3,0

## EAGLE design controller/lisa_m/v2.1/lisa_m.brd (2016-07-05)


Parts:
C1, C9: 4u7; 0603-CAP; PARTNO cap-cer-0603-4u7
C2, C3, C5, C7, C10, C11, C12, C14, C15, C26, C27, C36, C38: 100n; 0402-CAP; PARTNO cap-cer-0402-100n
C4, C6: 10p; 0402-CAP; PARTNO cap-cer-0402-10p
C13, C31: 10n; 0402-CAP; PARTNO cap-cer-0402-10n
C28: 1u; 0603-CAP; PARTNO cap-cer-0603-1u
C35: 470p; 0402-CAP; PARTNO cap-cer-0402-470p
C37, C39: 22u; 3528/B; PARTNO cap-tan-B-22u-16v
C42: 4n7; 0603-CAP; PARTNO cap-cer-0603-4n7
CON_ANALOG1: CONN_6-1-53398; PB-53398-06; PARTNO conn-picoblade-smd-0.05in-6-vert
CON_CAN/I2C1: CONN_7-1-53398; PB-53398-07; PARTNO conn-picoblade-smd-0.05in-7-vert
CON_GPIO: CONN_4-1-53398; PB-53398-04; PARTNO conn-picoblade-smd-0.05in-4-vert
CON_I2C2: CONN_4-1-53398; PB-53398-04; PARTNO conn-picoblade-smd-0.05in-4-vert
CON_SPI: CONN_7-1-53398; PB-53398-07; PARTNO conn-picoblade-smd-0.05in-7-vert
CON_UART1/5: CONN_6-1PB-53398-06_SMALL; PB-53398-06; PARTNO conn-picoblade-smd-0.05in-6-vert
CON_UART2, CON_UART3: CONN_4-1-53398; PB-53398-04; PARTNO conn-picoblade-smd-0.05in-4-vert
CON_USB: CONN_4-1-53047; PB-53047-04; PARTNO conn-picoblade-th-0.05in-4-vert
CON_USB_MICRO: ZX62-B-5PA; PARTNO conn-smd-usb-micro-b
D3: 1N5819; 0603-DIO; PARTNO diode-schottky-0603
IC9: LP2992 5V; SOT23-5; PARTNO vreg-sot-23-5-5v
JP1, JP2, JP3, JP6, JP7, JP8, JP9, JP12, JP13: 0/DNP; 0402-SQJMP; PARTNO res-0402-0
JP10, JP11: 0/DNP; 0603-RES; PARTNO res-0603-0
JTAG: PIN_HDR_EDG_1.27MM_5-2; FTSH-105-DV; PARTNO conn-smd-0.05in-5-2
L1: L; 0402-IND; PARTNO ferrite-0402-600
LED1: RED; 0402-LED; PARTNO led-0402-red
LED2: ORG; 0402-LED; PARTNO led-0402-org
LED3: GRN; 0402-LED; PARTNO led-0402-grn
LED4: YEL; 0402-LED; PARTNO led-0402-yel
LED5: RED; 0402-LED; PARTNO led-0402-grn
LEDVIN: GRN; 0402-LED; PARTNO led-0402-grn
LT_I2C2: PCA9306DP; TSSOP_B3; PARTNO ic-tssop8-level-trans
PH1, PH2, PH3, PH4: PH2X3; PH010-2-3
Q1: 12Mhz; ABM8; PARTNO xtal-abm8-12mhz
R1, R3, R6, R7, R17, R24, R26, R30: 10k; 0402-RES; PARTNO res-0402-10k
R4, R5, R11, R18, R23, R33, R34, R43, R44: 2k2; 0402-RES; PARTNO res-0402-2k2
R8, R10, R12, R37, R38: 300; 0402-RES; PARTNO res-0402-300
R25: 200k; 0402-RES; PARTNO res-0402-200k
R27, R28, R31, R39, R40, R41, R42, R45: 100R; 0402-RES; PARTNO res-0402-100
R55: 0/10k; 0402-RES; PARTNO res-0402-10k
R56: 0/DNP; 0402-RES; PARTNO res-0402-0
R58, R59: 60R/DNP; 0402-RES; PARTNO res-0402-60.4
R60, R61: 4k7/DNP; 0402-RES; PARTNO res-0402-4k7
SW1: MICROTACT_GND; PARTNO sw-tact-top-gnd-3.0-2.5
U1: MCP2551SN; SO-08; PARTNO ic-so8-can
U2: STM32-C-64; LQFP64; PARTNO ic-mcu-stm32f415rgt6
VREG1: MIC5209; SOIC8; PARTNO vreg-so8-3v3

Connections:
+3V3: C5.P$2 (2), C9.P$1 (1), C10.P$2 (2), C11.P$2 (2), C12.P$2 (2), C36.P$1 (1), C37.+, CON_ANALOG1.2, CON_GPIO.2, CON_I2C2.2, CON_SPI.2, CON_UART2.2, JP7.P$1 (1), JP9.P$1 (1), JTAG.1, L1.P$1 (1), LT_I2C2.2 (VREF1), R4.P$1 (1), R5.P$1 (1), R7.P$2 (2), R8.P$2 (2), R10.P$2 (2), R11.P$1 (1), R12.P$2 (2), R26.P$1 (1), R33.P$2 (2), R34.P$2 (2), R37.P$2 (2), R38.P$2 (2), U2.1 (VBAT), U2.19 (VDD4), U2.32 (VDD1), U2.48 (VDD2), U2.64 (VDD3), VREG1.3 (VOUT); also elsewhere on the board
+5V: C1.P$1 (1), C2.P$1 (1), C26.P$1 (1), CON_ANALOG1.3, IC9.5 (VOUT), JP3.P$2 (2), R25.P$2 (2), R43.P$2 (2), R44.P$2 (2), R56.P$2 (2), R60.P$1 (1), U1.3 (VDD)
ADC_1: CON_ANALOG1.4, U2.11 (PC3-ADC13/ETH_MII_TX_CLK)
ADC_2: CON_ANALOG1.5, U2.8 (PC0-ADC10)
ADC_3: CON_ANALOG1.6, U2.9 (PC1-ADC11/ETH_(R)MII_MDC)
BARO_DRDY: U2.26 (PB0-ADC8/TIM3CH3/ETH_MII_RXD2-TIM1CH2N)
BIND_BUT: R11.P$2 (2), SW1.2, U2.28 (PB2/BOOT1)
BOOT0: R30.P$2 (2), U2.60 (BOOT0)
CAN_CENTER: C42.P$2 (2), R58.P$2 (2), R59.P$1 (1), R60.P$2 (2), R61.P$1 (1)
CAN_H: CON_CAN/I2C1.5, R58.P$1 (1), U1.7 (CANH)
CAN_L: CON_CAN/I2C1.4, R59.P$2 (2), U1.6 (CANL)
CAN_RX: U1.4 (RXD), U2.61 (PB8-TIM4CH3/ETH_MII_TXD3-I2C1SCL/CAN1RX)
CAN_TX: U1.1 (TXD), U2.62 (PB9-TIM4CH4-I2C1SDA/CAN1TX)
EXTSPI_DRDY: CON_SPI.7, U2.27 (PB1-ADC9/TIM3CH4/ETH_MII_RXD3-TIM1CH3N)
EXTSPI_MISO: CON_SPI.4, U2.22 (PA6-SPI1MISO/ADC6/TIM3CH1-TIM1BKIN)
EXTSPI_MOSI: CON_SPI.3, U2.23 (PA7-SPI1MOSI/ADC7/TIM3CH2/ETH_MII_RX_DV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)
EXTSPI_SCK: CON_SPI.5, U2.21 (PA5-SPI1SCK/DAC2/ADC5)
EXTSPI_SS: CON_SPI.6, U2.20 (PA4-SPI1NSS/DAC1/USART2CK/ADC4-SPI3NSS/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)
GND: C1.P$2 (2), C2.P$2 (2), C3.P$2 (2), C4.P$1 (1), C5.P$1 (1), C6.P$2 (2), C7.P$1 (1), C9.P$2 (2), C10.P$1 (1), C11.P$1 (1), C12.P$1 (1), C13.P$2 (2), C14.P$1 (1), C15.P$2 (2), C26.P$2 (2), C27.P$1 (1), C28.P$2 (2), C31.P$1 (1), C35.P$2 (2), C36.P$2 (2), C37.-, C38.P$2 (2), C39.-, C42.P$1 (1), CON_ANALOG1.1, CON_CAN/I2C1.1, CON_GPIO.1, CON_I2C2.1, CON_SPI.1, CON_UART1/5.1, CON_UART1/5.4, CON_UART2.1, CON_UART3.1, CON_USB.4, CON_USB_MICRO.PIN_5 (5), IC9.2 (GND), JP12.P$2 (2), JP13.P$2 (2), JTAG.3, JTAG.5, JTAG.7, JTAG.9, LEDVIN.C, LT_I2C2.1 (GND), PH1.3, PH1.6 (3), PH2.3, PH2.6 (3), PH3.3, PH3.6 (3), PH4.3, PH4.6 (3), Q1.P$2, Q1.P$4, R1.P$2 (2), R18.P$2 (2), R30.P$1 (1), R55.P$1 (1), R61.P$2 (2), SW1.1, SW1.G (GND), U1.2 (VSS), U2.12 (VSSA), U2.18 (VSS4), U2.63 (VSS3), VREG1.5 (GND4), VREG1.6 (GND3), VREG1.7 (GND2), VREG1.8 (GND1); also elsewhere on the board
I2C2_SCL: CON_I2C2.3, R4.P$2 (2), U2.29 (PB10-I2C2SCL/USART3TX/ETH_MII_RX_ER-TIM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)
I2C2_SDA: CON_I2C2.4, R5.P$2 (2), U2.30 (PB11-I2C2SDA/USART3RX/ETH_(R)MII_TX_EN-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)
IMU_BARO_CS: U2.2 (PC13-TAMPER-RTC); also elsewhere on the board
IMU_MAG_INT: U2.3 (PC14-OSC32_IN); also elsewhere on the board
IMU_MPU_CS: U2.33 (PB12-SPI2NSS/I2S2WS/I2C2SMBA/USART3CK/T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); also elsewhere on the board
IMU_MPU_INT: U2.57 (PB5-I2C1SMBA/SPI3MOSI/ETH_(R)MII_PPS_OU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); also elsewhere on the board
IMU_SPI_MISO: U2.35 (PB14-SPI2MISO/USART3RTS/TIM1CH2N); also elsewhere on the board
IMU_SPI_MOSI: U2.36 (PB15-SPI2MOSI/I2S2SD/TIM1CH3N); also elsewhere on the board
IMU_SPI_SCK: U2.34 (PB13-SPI2SCK/I2S2CK/USART3CTS/TIM1CH1N/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); also elsewhere on the board
JTAG_RST: C27.P$2 (2), JTAG.10, R7.P$1 (1), U2.7 (NRST)
JTAG_TCK: JTAG.4, U2.49 (PA14/JTCK/SWCLK)
JTAG_TDI: JTAG.8, U2.50 (PA15/JTDI-SPI3NSS/I2S3WS-TIM2CH1ETR/SPI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)
JTAG_TDO: JTAG.6, U2.55 (PB3/JTDO-SPI3SCK/I2S3CK-TIM2CH2/TRACESW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)
JTAG_TMS: JTAG.2, U2.46 (PA13/JTMS/SWDIO)
LED1: LED1.C, U2.41 (PA8-USART1CK/OTG_FS_SOF/MCO/TIM1CH1)
LED2: CON_GPIO.4, LED2.C, U2.56 (PB4/JNTRST-SPI3MISO-TIM3CH1/SPI1MISO)
LED3: LED3.C, U2.10 (PC2-ADC12/ETH_MII_TXD2)
LED4: LED4.C, U2.25 (PC5-ADC15ETH_(R)MII_RXD1)
LED5: LED5.C, U2.4 (PC15-OSC32_OUT)
LT_I2C1_SCL: CON_CAN/I2C1.6, JP10.P$2 (2), LT_I2C2.6 (SCL2), R44.P$1 (1)
LT_I2C1_SDA: CON_CAN/I2C1.7, JP11.P$2 (2), LT_I2C2.5 (SDA2), R43.P$1 (1)
unnamed: R55.P$2 (2), R56.P$1 (1), U1.8 (RS)
unnamed: LED1.A, R10.P$1 (1)
unnamed: C13.P$1 (1), IC9.4 (BYPASS)
unnamed: C35.P$1 (1), VREG1.4 (BYP)
unnamed: C15.P$1 (1), LT_I2C2.7 (VREF2), LT_I2C2.8 (EN), R25.P$1 (1)
unnamed: LED2.A, R8.P$1 (1)
unnamed: LEDVIN.A, R23.P$1 (1)
unnamed: LED5.A, R12.P$1 (1)
unnamed: LED4.A, R37.P$1 (1)
unnamed: LED3.A, R38.P$1 (1)
OSC_IN: C4.P$2 (2), Q1.P$3, U2.5 (PD0-OSC_IN-CAN1RX)
OSC_OUT: C6.P$1 (1), Q1.P$1, U2.6 (PD1-OSC_OUT-CAN1TX)
PC12: CON_GPIO.3, U2.53 (PC12-USART5TX-USART3CK/SPI3MOSI/I2S3SD)
S1: PH1.1, R41.P$1 (1)
S2: PH1.4 (1), R42.P$1 (1)
S3: PH2.1, R45.P$1 (1)
S4: PH2.4 (1), R27.P$1 (1)
S5: PH3.1, R28.P$1 (1)
S6: PH3.4 (1), R31.P$1 (1)
S7: PH4.1, R39.P$1 (1)
S8: PH4.4 (1), R40.P$1 (1)
SERVO_1: R41.P$2 (2), U2.37 (PC6-I2S2MCK-TIM3CH1)
SERVO_2: R42.P$2 (2), U2.38 (PC7-I2S3MCK-TIM3CH2)
SERVO_3: R45.P$2 (2), U2.39 (PC8-TIM3CH3)
SERVO_4: R27.P$2 (2), U2.40 (PC9-TIM3CH4)
SERVO_5: R28.P$2 (2), U2.14 (PA0-WKUP/USART2CTS/ADC0/TIM2CH1ETR/TIM5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)
SERVO_6: R31.P$2 (2), U2.15 (PA1-USART2RTS/ADC1/TIM5CH2/TIM2CH2/ETH_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)
SERVO_7/I2C1_SCL: JP10.P$1 (1), LT_I2C2.3 (SCL1), R33.P$1 (1), R39.P$2 (2), U2.58 (PB6-I2C1SCL/TIM4CH1-USART1TX/CAN2TX)
SERVO_8/I2C1_SDA: JP11.P$1 (1), LT_I2C2.4 (SDA1), R34.P$1 (1), R40.P$2 (2), U2.59 (PB7-I2C1SDA/TIM4CH2-USART1RX)
SERVO_BUS: JP1.P$1 (1), PH1.2, PH1.5 (2), PH2.2, PH2.5 (2), PH3.2, PH3.5 (2), PH4.2, PH4.5 (2)
U1_U5_POW: CON_UART1/5.2, CON_UART1/5.5, JP8.P$2 (2), JP9.P$2 (2), R6.P$1 (1), R24.P$1 (1)
U3_POW: CON_UART3.2, JP6.P$2 (2), JP7.P$2 (2), R3.P$1 (1)
UART1_RX: CON_UART1/5.3, R24.P$2 (2), U2.43 (PA10-USART1RX/TIM1CH3/OTG_FS_ID)
UART2_RX: CON_UART2.4, R26.P$2 (2), U2.17 (PA3-USART2RX/TIM5CH4/ADC3/TIM2CH4/ETH_M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)
UART2_TX: CON_UART2.3, U2.16 (PA2-USART2TX/TIM5CH3/ADC2/TIM2CH3/ETH_(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)
UART3_RX: CON_UART3.4, R3.P$2 (2), U2.52 (PC11-USART4RX-USART3RX/SPI3MISO)
UART3_TX: CON_UART3.3, U2.51 (PC10-USART4TX-USART3TX/SPI3SCK/I2S3CK)
UART5_RX: CON_UART1/5.6, R6.P$2 (2), U2.54 (PD2-TIM3ETR/USART5RX)
USB_DM: CON_USB.2, CON_USB_MICRO.PIN_2 (2), U2.44 (PA11-USART1CTS/CAN1RX/OTG_FS_DM/TIM1CH4)
USB_DP: CON_USB.3, CON_USB_MICRO.PIN_3 (3), U2.45 (PA12-USART1RTS/CAN1TX/OTG_FS_DP/TIM1ETR)
USB_VBUS: CON_USB.1, CON_USB_MICRO.PIN_1 (1), D3.A, R1.P$1 (1), U2.42 (PA9-USART1TX/TIM1CH2/OTG_FS_VBUS)
VDDA: C28.P$1 (1), C31.P$2 (2), L1.P$2 (2), U2.13 (VDDA)
VREF: U1.5 (VREF)
VSS1: C7.P$2 (2), JP12.P$1 (1), U2.31 (VSS1)
VSS2: C14.P$2 (2), JP13.P$1 (1), U2.47 (VSS2)
V_BAT: CON_CAN/I2C1.2, JP2.P$2 (2), R17.P$1 (1)
V_BAT_MEAS: R17.P$2 (2), R18.P$1 (1), U2.24 (PC4-ADC14/ETH_(R)MII_RXD0)
V_IN: C3.P$1 (1), C38.P$1 (1), C39.+, CON_CAN/I2C1.3, D3.C, IC9.1 (VIN), IC9.3 (ON/OFF), JP1.P$2 (2), JP2.P$1 (1), JP3.P$1 (1), JP6.P$1 (1), JP8.P$1 (1), R23.P$2 (2), VREG1.1 (ENABLE), VREG1.2 (VIN); also elsewhere on the board

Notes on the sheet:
Servos Connectors
3V3 SUPPLY
5V SUPPLY
License: CC-BY-SA 3.0
http://creativecommons.org/licenses/by-sa/3.0
(C) 2010-2014 Piotr Esden-Tempski <piotr@esden.net>
(C) 2010-2011 Antoine Drouin <poinix@gmail.com>
(C) 2011 Richard Hatano <rhatano@jobyenergy.com>
(C) 2011 Joby Robotics <info@jobyrobotics.com>
(C) 2011 Transition Robotics <info@transition-robotics.com>
Bind Button
1BitSquared LLC
JTAG
SWDIO
SWCLK
TRACESWO
MCU
LEDS
USB
SPI
I2C2
ANALOG1
GPIO1
UART3
UART2
RC RX\
CAN/I2C1
I2C1_LEVEL_SHIFTER
CAN_TRANSCIEVER
Lisa/M(X) V2.1


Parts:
C101, C108, C110, C112: 100n; 0402-CAP; PARTNO cap-cer-0402-100n
C104: 2u2; 0603-CAP; PARTNO cap-cer-0603-2u2
C105, C113: 4u7; 0603-CAP; PARTNO cap-cer-0603-4u7
C106: 10n; 0402-CAP; PARTNO cap-cer-0402-10n
C109: 2n2; 0402-CAP; PARTNO cap-cer-0402-2n2
C114: 220n; 0603-CAP; PARTNO cap-cer-0603-220n
IC101: LP2992; SOT23-5; PARTNO vreg-sot23-5-3v3
IC102: MS5611; QFN-MS5611; PARTNO ic-sensr-ms5611
L101: L; 0402-IND; PARTNO ferrite-0402-600
R2, R9: 2k2; 0402-RES; PARTNO res-0402-2k2
R29: 10k; 0402-RES; PARTNO res-0402-10k
U102: MPU-6000; QFN24-NO-PAD; PARTNO ic-sensr-mpu6000
U103: HMC5883L; LPCC16-HMC5883L; PARTNO ic-sensr-hmc5883l

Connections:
+3V3: R2.P$2 (2), R9.P$2 (2), R29.P$1 (1); also elsewhere on the board
BARO_+3V3: C101.P$1 (1), IC102.1 (VDD), L101.P$1 (1)
GND: C101.P$2 (2), C104.P$2 (2), C105.P$2 (2), C106.P$1 (1), C108.P$2 (2), C109.P$2 (2), C110.P$2 (2), C112.P$2 (2), C113.P$2 (2), IC101.2 (GND), IC102.2 (PS), IC102.3 (GND), U102.1 (CLKIN), U102.11 (FSYNC), U102.18 (GND), U103.9 (GND), U103.11 (GND2); also elsewhere on the board
IMU+3V3: C105.P$1 (1), C108.P$1 (1), C112.P$1 (1), IC101.5 (OUT), L101.P$2 (2), U102.13 (VDD), U103.2 (VDD), U103.4 (S1), U103.13 (VDDIO)
IMU_BARO_CS: IC102.4 (!CSB), IC102.5 (!CSB); also elsewhere on the board
IMU_MAG_INT: U103.15 (DRDY); also elsewhere on the board
IMU_MPU_CS: U102.8 (!CS); also elsewhere on the board
IMU_MPU_INT: R29.P$2 (2), U102.12 (INT); also elsewhere on the board
IMU_SPI_MISO: IC102.6 (SDO), U102.9 (AD0/SDO); also elsewhere on the board
IMU_SPI_MOSI: IC102.7 (SDI/SDA), U102.24 (SDA/SDI); also elsewhere on the board
IMU_SPI_SCK: IC102.8 (SCLK), U102.23 (SCL/SCLK); also elsewhere on the board
unnamed: C109.P$1 (1), U102.20 (CPOUT)
unnamed: C110.P$1 (1), U102.10 (REGOUT)
unnamed: C113.P$1 (1), U103.10 (C1)
unnamed: C106.P$2 (2), IC101.4 (ADJ)
unnamed: C114.P$2 (2), U103.8 (SETP)
unnamed: C114.P$1 (1), U103.12 (SETC)
SCL: R9.P$1 (1), U102.7 (AUX_CL), U103.1 (SCL)
SDA: R2.P$1 (1), U102.6 (AUX_DA), U103.16 (SDA)
V_IN: C104.P$1 (1), IC101.1 (IN), IC101.3 (EN); also elsewhere on the board

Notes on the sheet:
3V3 DIGITAL
Magnetometer
Accelerometer & Gyroscope
Presure
License: CC-BY-SA 3.0
http://creativecommons.org/licenses/by-sa/3.0
(C) 2010-2014 Piotr Esden-Tempski <piotr@esden.net>
(C) 2011 Richard Hatano <rhatano@jobyenergy.com>
(C) 2011 Joby Robotics <info@jobyrobotics.com>
(C) 2011 Transition Robotics <info@transition-robotics.com>
(C) 2010-2011 Antoine Drouin <poinix@gmail.com>
Lisa/M(X) V2.1



Board: 4 copper layers, 52.7 x 36.3 mm, 120 parts (59 on the bottom side), 96 nets.

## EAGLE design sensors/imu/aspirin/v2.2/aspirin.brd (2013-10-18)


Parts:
ASP1: ASPIRIN; ASPIRIN_CASTELLATED; PARTNO pcb-aspirin
C1, C8, C10, C11, C12: 100n; 0402-CAP; PARTNO cap-cer-0402-100n
C4: 2.2uF/Low ESR; 0603-CAP; PARTNO cap-cer-0603-2u2
C5, C13: 4.7uF/10V/Low ESR; 0603-CAP; PARTNO cap-cer-0603-4u7
C6: 10nF; 0402-CAP; PARTNO cap-cer-0402-10n
C9: 2n2; 0402-CAP; PARTNO cap-cer-0402-2n2
C14: 220n/Low ESR; 0603-CAP; PARTNO cap-cer-0603-220n
IC1: LP2992; SOT23-5; PARTNO vreg-sot-23-5-3v3
IC2: MS5611; QFN-MS5611; PARTNO sensr-qfn-8-baro
IC3: >4KBIT SERIAL EEPROM HALF PROTECT; SOT23-5; PARTNO ic-sot-23-5-4k-eeprom
JP4, JP5: 0/DNP; 0402-SQJMP; PARTNO res-0402-0
L1: INDUCTOR-0603; 0603-IND; PARTNO ferrite-0603-600ohm
R1, R2, R3: 4k7; 0402-RES; PARTNO res-0402-4k7
U1: HMC5883; PLCC16-HMC5883; PARTNO sensr-plcc-16-mag
U2: MPU-6000; QFN24-NO-PAD; PARTNO sensr-qfn-24-acc-gyro
U$2: 1B2-NEW-LOGO-3MM

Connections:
+3V3: C5.P$1 (1), C8.P$1 (1), C11.P$1 (1), C12.P$1 (1), IC1.5 (OUT), IC3.4 (VCC), L1.P$2 (2), R1.P$1 (1), R2.P$1 (1), R3.P$2 (2), U1.2 (VDD), U1.4 (S1), U1.13 (VDDIO), U2.13 (VDD)
+6V5: ASP1.2 (+6V5), C4.P$1 (1), IC1.1 (IN), IC1.3 (EN)
BARO_+3V3: C1.P$1 (1), IC2.1 (VDD), L1.P$1 (1)
BARO_CS: ASP1.8 (GYRO_CS), IC2.4 (!CSB), IC2.5 (!CSB)
GND: ASP1.1 (GND), ASP1.7 (GND), ASP1.14 (GND), C1.P$2 (2), C4.P$2 (2), C5.P$2 (2), C6.P$1 (1), C8.P$2 (2), C9.P$2 (2), C10.P$2 (2), C11.P$2 (2), C12.P$2 (2), C13.P$2 (2), IC1.2 (GND), IC2.2 (PS), IC2.3 (GND), IC3.2 (VSS), U1.9 (GND), U1.11 (GND), U2.1 (CLKIN), U2.11 (FSYNC), U2.18 (GND)
MAG_INT: ASP1.9 (GYRO_INT), U1.15 (DRDY)
MISO: ASP1.3 (MISO), IC2.6 (SDO), U2.9 (AD0/SDO)
MOSI: ASP1.4 (MOSI), IC2.7 (SDI/SDA), U2.24 (SDA/SDI)
MPU_CS: ASP1.12 (ACC_CS), U2.8 (!CS)
MPU_INT: ASP1.6 (MAG_INT), U2.12 (INT)
unnamed: C9.P$1 (1), U2.20 (CPOUT)
unnamed: C10.P$1 (1), U2.10 (REGOUT)
unnamed: C13.P$1 (1), U1.10 (C1)
unnamed: IC3.5 (WP), R3.P$1 (1)
unnamed: C6.P$2 (2), IC1.4 (ADJ)
unnamed: C14.P$2 (2), U1.8 (SETP)
unnamed: C14.P$1 (1), U1.12 (SETC)
SCK: ASP1.5 (SCK), IC2.8 (SCLK), U2.23 (SCL/SCLK)
SCL: JP5.P$2 (2), R1.P$2 (2), U1.1 (SCL), U2.7 (AUX_CL)
SDA: JP4.P$2 (2), R2.P$2 (2), U1.16 (SDA), U2.6 (AUX_DA)
XSCL: ASP1.10 (SCL), IC3.1 (SCL), JP5.P$1 (1)
XSDA: ASP1.11 (SDA), IC3.3 (SDA), JP4.P$1 (1)

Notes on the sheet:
3V3 DIGITAL
Gyroscope
EEPROM
Magnetometer
Accelerometer
2.2
Presure
License: CC-BY-SA 3.0
http://creativecommons.org/licenses/by-sa/3.0
(C) 2010-2013 Piotr Esden-Tempski <piotr@esden.net>
(C) 2010-2011 Antoine Drouin <poinix@gmail.com>
(C) 2011 Richard Hatano <rhatano@jobyenergy.com>
(C) 2011-2012 Transition Robotics <info@transition-robotics.com>
(C) 2013 1BitSquared <info@1bitsquared.com>


Board: 4 copper layers, 18.8 x 15.5 mm, 24 parts (0 on the bottom side), 22 nets.

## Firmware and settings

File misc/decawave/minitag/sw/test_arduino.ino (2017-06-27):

// the setup function runs once when you press reset or power the board
void setup() {
  // initialize digital pin LED_BUILTIN as an output.
  pinMode(14, OUTPUT);
}

// the loop function runs over and over again forever
void loop() {
  digitalWrite(14, HIGH);   // turn the LED on (HIGH is the voltage level)
  delay(1000);                       // wait for a second
  digitalWrite(14, LOW);    // turn the LED off by making the voltage LOW
  delay(1000);                       // wait for a second
}

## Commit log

2011-11-24 Initial commit after a coarce cleanup. For older revisions check the hardware svn repository on Savannah. http://svn.savannah.nongnu.org/viewvc/paparazzi-hardware/trunk/?root=paparazzi
    [AMI_601.brd, AMI_601.sch, BOM.ods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]
2011-11-24 Reorganized sensor directory a bit.
    [aspirin.brd, aspirin.sch, aspirin_carrier_board.brd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]
2011-12-01 Starting work on lia v1.0 controller board.
    It is based on lisa/m and uses throughole 0.1" pin headers instead of
    molex picoblade.
    [lia.brd, lia.sch]
2011-12-01 Added BEC balance inline resistors.
    [lia.brd, lia.sch]
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2011-12-05 Starting revised aspirn v2.1. Added i2c jumpers.
    [aspirin.brd, aspirin.sch]
2011-12-05 Added MS5611 to the schematic.
    [aspirin.brd, aspirin.sch]
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2011-12-05 Added pull-ups to local i2c and it is probably a good idea to supply the pressure sensor with power...
    * The i2c pullups are not quoted in any of the mpu-6000 datasheets
    explicitely there is a very unlikely chance that they may not needed.
    Needs to be tested.
    * Connected VDD to +3v3 (seriously no comment ...)
    [aspirin.brd, aspirin.sch]
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2012-01-13 Started Lisa/M V2.1. Swapped the labeling of Analog1 and Analog2 connectors to be more sensible and adhering to the documentation in the wiki. fixes #5
    [lisa_m.brd, lisa_m.sch]
2012-01-13 Swapped labeling of Analog1 and Analog2 connectors to make the naming more sensible.
    [lia.brd, lia.sch]
2012-01-13 Connected the pressure sensor to the MPU-6000. fixes #1
    Now using the auxilary I2C interface instead of the host MCU SPI.
    This will allow reading out of almost all sensor data in one time
    syncronous spi data burst from the MPU-6000.
    [aspirin.brd, aspirin.sch]
2012-01-13 Corrected the coordinate system symbol on the silkscreen. fixes #2
    [aspirin.brd]
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2012-01-13 Increased size of the magnetometer caps to improve performance. fixes #4
    The new size of the HMC magnetometer caps is 0603 otherwise it is
    difficult to get low esr versions of those to gain good performance.
    [aspirin.brd, aspirin.sch]
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2012-01-17 Removed three unnecessary solderstop windows. Fixed solderstop layer comments.
    [lia.brd, lia_teardrops.brd]
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2012-01-18 Some more tweaks for DRC satisfaction. Regenerated teardrops.
    [lia.brd, lia_teardrops.brd]
2012-01-18 Some modifications to satisfy DRC and generated teardropped version.
    [aspirin-teardrops.brd, aspirin.brd]
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2012-01-20 Updated bom-ex id designators to be more readable, unique and consistent.
    [lisa_m.brd, lisa_m.sch]
2012-01-20 Updated bom-ex id's to be more consistent, readable and unique.
    [lia.brd, lia.sch]
2012-01-20 Some last minute DRC changes for prototype production run.
    [aspirin.brd]
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2012-01-21 Replaced some blue led's with amber and green ones.
    [lia.brd, lia.sch, lisa_m.brd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]
2012-01-23 Changed the resistors for non blue leds to 300ohm.
    [lia.brd, lia.sch, lisa_m.brd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]
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2012-01-27 More BOM tweaking, also readded the micro USB to lia.
    [lia.brd, lia.sch, lisa_m.brd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]
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2012-02-01 Removed fiducials on the board, we have them on the rails.
    [aspirin.brd]
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2012-02-01 Updated teardropped aspirin and switched gerber generation to use that instead.
    [aspirin-teardrops.brd, layout.cfg]
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2012-02-04 Went back to 4layer design. Removed restrict's under the mag and mpu. Removed traces under the MPU based on datasheet recommendations.
    [aspirin.brd]
2012-02-04 Adding alternative routing of aspirin 2.1. May be a bit cleaner? GYRO_INT and MAG_INT signals are swapped and magnetometer and MPU positions are swapped too.
    [aspirin_alt.brd, aspirin_alt.sch]
2012-02-06 Converted all eagle files to Eagle 6 format.
    [AMI_601.brd, AMI_601.sch, adxrs300_breakout.brd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]
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2012-02-06 Aspirin alt design is cleaner, made it the official routing of v2.1.
    [aspirin.brd, aspirin.sch, aspirin_alt.brd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]
2012-02-06 Switched gerber generation back to non teardropped PCB. As well as changed the panel geometry.
    [layout.cfg]
2012-02-06 Reapproved DRC errors.
    [aspirin.brd]
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2012-02-15 Moved and resized the coordinate system symbol on the silkscreen.
    [aspirin.brd]
2012-02-15 Moved mag SDA via to connect both sides of the bottom 3V3 plane.
    [aspirin.brd]
2012-02-16 Some minor cleanups and touchups. Renamed signal silkscreen legend's to better reflect reality.
    [aspirin.brd, aspirin.sch]
2012-02-17 Renamed ACC_CS to MPU_CS and changed panel to 3x3.
    [aspirin.brd, aspirin.sch]
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2012-03-05 Minor final fixes before going into assembly.
    [aspirin.brd, aspirin.sch]
2012-03-13 Added SparkFun based xbee carrier with picoblade connector.
    [xbee_carrier.brd, xbee_carrier.sch]
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2012-03-13 Removed solder stop from vias on the xbee_carrier.
    [xbee_carrier.brd]
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2012-05-07 - switched analog1 and analog2 connector labels on schematic and silkscreen - changed LED labels on schematic to be more intuitive and match software defines - changed power led to LEDVIN from LED4 (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
    [lisa_m.brd, lisa_m.sch]
2012-05-07 updated the uart1/3 labeling on silkscreen, unsmashed some LED labels
    [lisa_m.brd, lisa_m.sch]
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2012-05-07 Initial commit of lia 1.1.
    Changes from 1.0 to now:
    * Replaced pin header with micro usb connector
    * Rotated top silkscreen labels 180 to show up readable in the quadshot
    airframe.
    * Repositioned the side pinheaders to fit into a breadboard.
    * Removed pressure sensor footprint.
    * Improved silkscreen and synchronized with Lisa/M 2.0 r1
    * Probably few others that I forgot. :) (I know I should commit more
    often)
    [lia.brd, lia.sch]
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2012-05-21 Fixed the corner pin intended for GYRO_CS to be disconnected from ground and labeled RESV on the pcb.
    [aspirin.brd, aspirin.sch]
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2012-05-23 Added bom-x attributes and connected the tantalum to ground.
    [xbee_carrier.brd, xbee_carrier.sch]
2012-06-21 Added a proposal for an improved Aspirin V2.2.
    [aspirin.brd, aspirin.sch]
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2013-03-02 Add Melexis MLX90614 infrared thermometer with I2C interface.
    [mlx90614_small.brd, mlx90614_small.sch]
2013-03-02 Add Sensirion SHT75 adapter board for proprietary digital interface
    [sht75_small.brd, sht75_small.sch]
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2013-03-17 small corrections, add pdf schematics: i2c_multi, sht75, mlx90614 and sht25
    [mlx90614_small.sch, sht75_small.sch]
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2013-10-18 Updated led footprints to have placement information about orientation.
    [lisa_m.brd, lisa_m.sch, lisa_m_teardrops.brd]
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2014-01-30 fix SHT75 humidity board, add 90 degrees version of SHT75 board
    [sht75_small.brd, sht75_small_90deg.brd, sht75_small_90deg.sch]
2014-04-11 STM32F4 Daughterboard initioal
    Daughterboard for the STM32F4 Discovery, only tht components
    [stm32f4discovery_daughterboard.dsn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]
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2014-05-02 fixed align of the main header
    The Main pin header (for the dosvocery board) was offset in the previous
    version.
    [stm32f4discovery_daughterboard.dsn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]
2015-07-31 added .pro and dxf outline
    Updated with 2015-07-30 6023 on Windows. Added DXF file containing board
    outline + holes. Added KiCAD project file.
    [stm32f4discovery_daughterboard.sch, stm32f4discovery_daughterboard_outline.dxf]
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2016-05-04 Added prototype of connector shield Lisa/S with Walkera Genius CPv2
    [lisashield-NPTH.drl, lisashield.drl, lisashield.gbl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]
2016-07-05 Updated V2.1 Lisa/M(X) hardware to the final production version.
    [lisa_m.brd, lisa_m.sch]
2016-09-18 Lia breakout board (#22)
    * Lia breakout board for HITL and testing
    * Box for the Lia breakout board
    [BOM_lia_breakout.csv, Lia_Breakout_Box_Bottom.STL, Lia_Breakout_Box_Top.STL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]
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

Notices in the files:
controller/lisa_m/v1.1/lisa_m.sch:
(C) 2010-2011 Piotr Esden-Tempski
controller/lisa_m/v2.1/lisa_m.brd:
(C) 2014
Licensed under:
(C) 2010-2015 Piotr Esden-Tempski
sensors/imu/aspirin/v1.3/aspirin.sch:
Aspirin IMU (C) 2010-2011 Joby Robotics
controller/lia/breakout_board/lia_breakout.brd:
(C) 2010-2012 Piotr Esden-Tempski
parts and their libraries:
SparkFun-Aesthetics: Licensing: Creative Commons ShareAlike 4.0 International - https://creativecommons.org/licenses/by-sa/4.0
